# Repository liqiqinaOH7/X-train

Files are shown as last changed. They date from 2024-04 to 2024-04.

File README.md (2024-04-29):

## 圣诞小火车奇遇之旅

这是一份技术文档汇总，主要介绍了圣诞小火车的硬件、机械结构、嵌入式代码等。

- 一些简单的介绍可以通过设计报告、视频和预提交ppt（https://1drv.ms/p/c/84c9984635f4f820/Ec5dhPh6r1hGjR61JKherjkBSfVEN543lnbwKaZI-xJIgA?e=UAQMFG）等方式了解。
- 电源、硬件、机械结构部分详细介绍请访问文档：
https://xn4zlkzg4p.feishu.cn/wiki/TbJOwzE71iRRNpkO2xwcQ5TinEe?from=from_copylink
- 嵌入式部分代码分为小车部分和中控板部分，具体代码在相应文件夹内。
- 机械结构的工程文档（Fusion360）可以在3D_Design文件夹内找到。

English:

This is a summary of the hardware, mechanical structure, and embedded code of the Christmas car.

- Some simple introductions can be obtained by watching design reports, videos, and pre-submitted ppts (https://1drv.ms/p/c/84c9984635f4f820/Ec5dhPh6r1hGjR61JKherjkBSfVEN543lnbwKaZI-xJIgA?e=UAQMFG).
- For more detailed information about power, hardware, and mechanical structure, please visit the documentation: https://xn4zlkzg4p.feishu.cn/wiki/TbJOwzE71iRRNpkO2xwcQ5TinEe?from=from_copylink
- The embedded code is divided into the car and the control board, and the specific code can be found in the corresponding folder.
- The mechanical structure's engineering documentation (Fusion360) can be found in the 3D_Design folder.

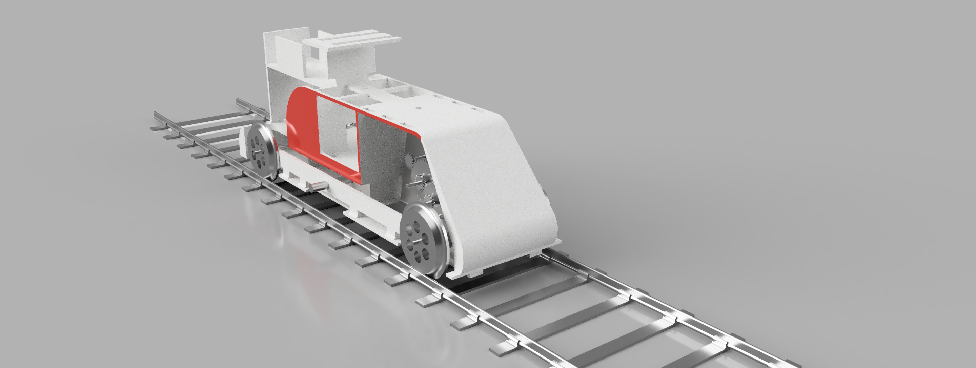
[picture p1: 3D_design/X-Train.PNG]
X-Train


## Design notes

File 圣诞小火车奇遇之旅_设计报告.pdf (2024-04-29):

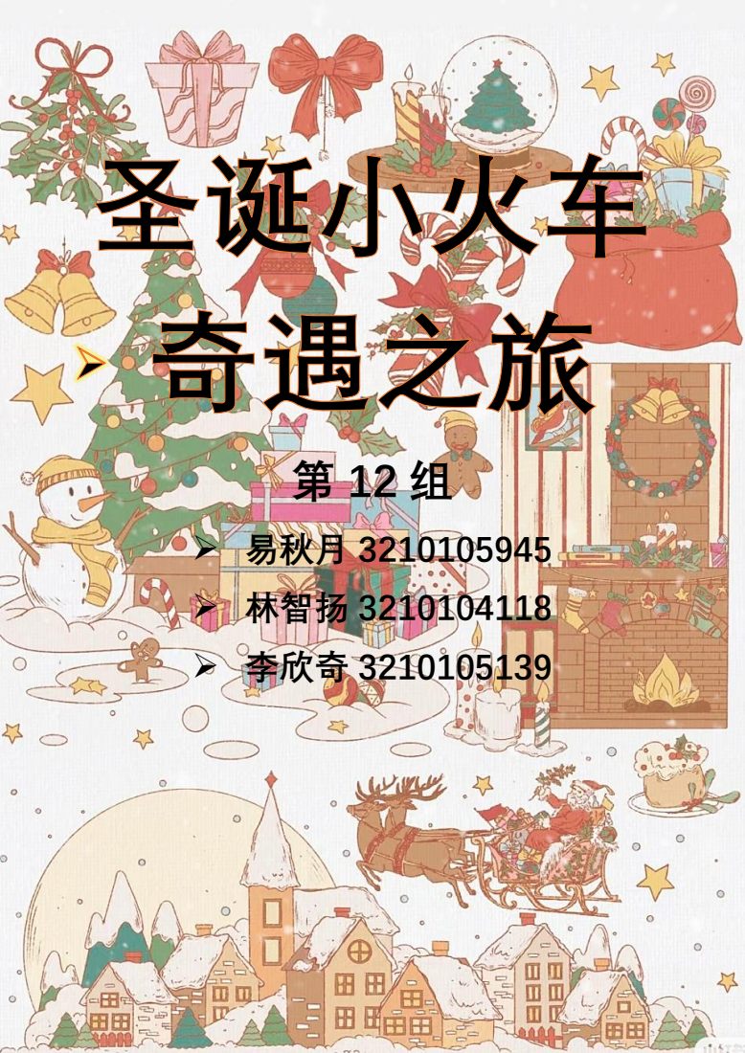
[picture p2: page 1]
➢ 易秋月 3210105945; ➢ 林智扬 3210104118; ➢ 李欣奇 3210105139

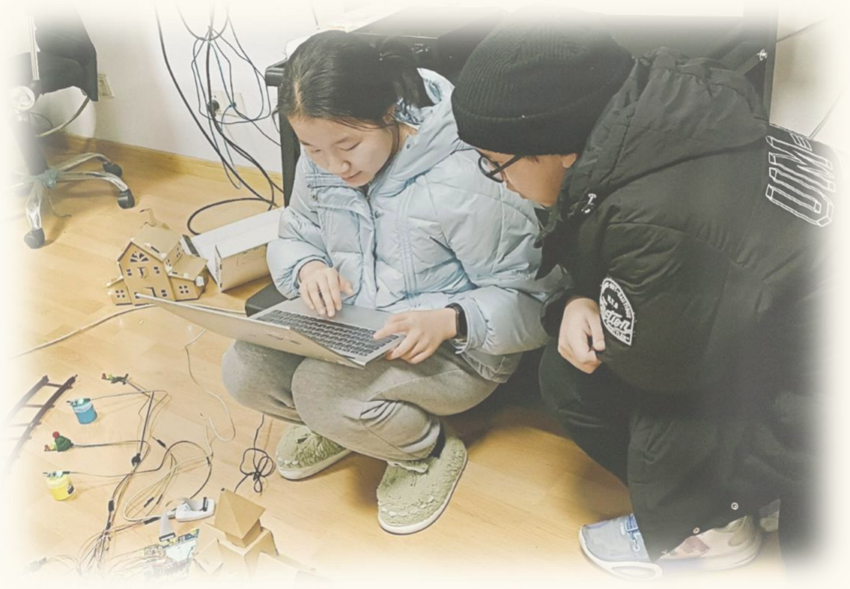
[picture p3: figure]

目录

目录

# 微控制器介绍

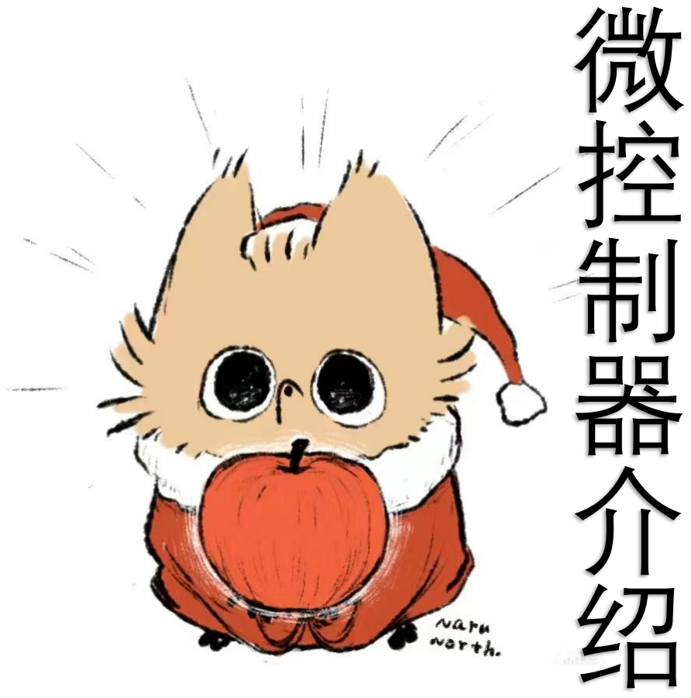
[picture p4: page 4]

## 一、微控制器介绍

1、ARM Cortex-M 系列微控制器概况：

ARM 公司从 ARMv6-ARMv7 时代开始 ARM 开始使用 A、R、M 系列来命名其新的处理器。

A 系列为应用处理器（Application Processor），其中 A 可以理解为 Application，面

向移动计算，智能手机，服务器等市场的的高端处理器。这类处理器运行在很高的时钟频率

（超过 1GHz），支持像 Linux，Android，MS Windows 和移动操作系统等完整操作系统需要

的内存管理单元（MMU）。如果规划开发的产品需要运行上述其中的一个操作系统，需要选择

ARM 应用处理器.

R 系列为实时处理器（Real-time Processors），其中 R 为 RealTime，面向实时应用的

高性能处理器系列，例如硬盘控制器，汽车传动系统和无线通讯的基带控制。多数实时处理

器不支持 MMU，不过通常具有 MPU、Cache 和其他针对工业应用设计的存储器功能。实时处

理器运行在比较高的时钟频率（例如 200MHz 到 >1GHz ），响应延迟非常低。虽然实时处理

器不能运行完整版本的 Linux 和 Windows 操作系统，但是支持大量的实时操作系统（RTOS）。

M系列为微控制器处理器（MicrocontrollerProcessors），其中M指的是Microcontroler

目前主要有 M0、M0+、M3、M4、M7 以及新发布不久的基于 ARMv8-M 构架的 M23、M33，其中

M23 为 M0&M0+的升级，M33 为 M3、M4 的升级。微控制器处理器通常设计成面积很小和能效

比很高。通常这些处理器的流水线很短，最高时钟频率很低（虽然市场上有此类的处理器可

以运行在 200Mhz 之上）。并且，新的 Cortex-M 处理器家族设计的非常容易使用。因此，

ARM 微控制器处理器在单片机和深度嵌入式系统市场非常成功和受欢迎。性能天梯如下图：

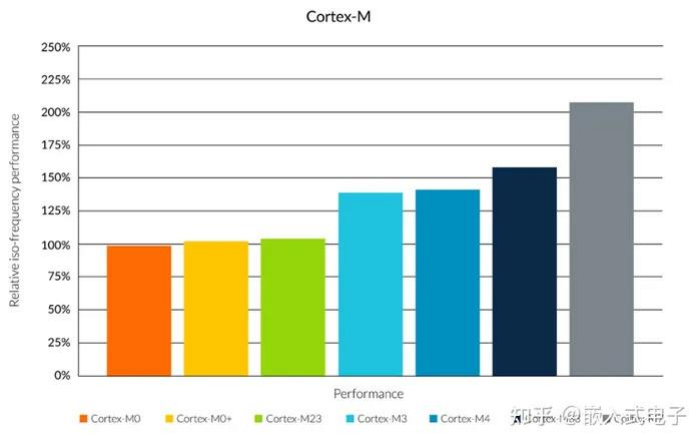
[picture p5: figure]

图 1 性能天梯对比

上图为同等主频下，各个内核可以提供的运算性能的大概的对比关系，评判一个处理器

处理性能一直是一个难题，有很多的评判标准，上图是 ARM 官网提供的，Cortex-M 系列在

ARM 官网上一直以 Coremark 分数为主要评测标准，可作为参考，真实的性能对比需要具体

应用。

2、Cortex-M 处理器家族

Cortex-M 处理器家族更多的集中在低性能端，但是这些处理器相比于许多微控制器使

用的传统处理器性能仍然很强大。例如，Cortex-M4 和 Cortex-M7 处理器应用在许多高性

能的微控制器产品中，最大的时钟频率可以达到 400Mhz。

当然，性能不是选择处理器的唯一指标。在许多应用中，低功耗和成本是关键的选择指

标。因此，Cortex-M 处理器家族包含各种产品来满足不同的需求：

Cortex-M0 | 面向低成本，超低功耗的微控制器和深度嵌入应用的非常小的处理器 (最小 12K 门电路)
Cortex-M0+ | 针对小型嵌入式系统的最高能效的处理器，与 Cortex-M0 处理器接近 的尺寸大小和编程模式但是具有扩展功能，如单周期 I/O 接口和向量 表重定位功能
Cortex-M1 | 针对 FPGA 设计优化的小处理器，利用 FPGA 上的存储器块实现了紧横 合内存 (TCM)。和 Cortex-M0 有相同的指令集
Cortex-M3 | 针对低功耗微控制器设计的处理器，面积小但是性能强劲，支持可以处 理器快速处理复杂任务的丰富指令集。具有硬件除法器和乘加指令 (MAC).并且，M3 支持全面的调试和跟踪功能使软件开发者可以快速的 开发他们的应用
Cortex-M4 | 不但具备 Cortex-M3 的所有功能，并且扩展了面向数字信号处理(DSP) 的指令集，比如单指今多数据指令(SMID)和更快的单周期 MAC 操作此 外，它还有一个可选的支持 IEEE754 浮点标准的单精度浮点运算单元
Cortex-M7 | 针对高端微控制器和数据处理密集的应用开发的高性能处理器。具备 Cortex-M4 支持的所有指令功能，扩展支持双精度浮点运算，并且具备 扩展的存储器功能，例如 Cache 和紧耦合存储器(TCM)
Cortex-M23 | 面向超低功耗，低成本应用设计的小尺寸处理器，和 Cortex-MO 相 似，但是支持各种增强的指令集和系统层面的功能特性。M23 还支持 TrustZone 安全扩展
Cortex-M33 | 主流的处理器设计，与之前的 Cortex-M3 和 Cortex-M4 处理器类似， 但系统设计更灵活，能耗比更高效，性能更高。M33 还支持 TrustZone 安全扩展

3、微处理器为 Cortex-M3 的微控制器 STM32F103ZE

- 核心：STM32F103ZE 采用 ARM Cortex-M3 32 位处理器核心，运行频率高达 72 MHz。
- 存储：具有 512 KB 的闪存存储器和 64 KB 的静态随机存取存储器（SRAM）。
- 外设：包括多个通用定时器、串行通信接口（SPI、I2C）、通用异步收发器（USART）、

模拟-数字转换器（ADC）等。

- 连接：支持多种外部连接接口，如 USB、CAN、以太网等。
- 电源：具有多种电源管理功能，包括低功耗模式和多种电源模式选择。
- 封装：该微控制器的封装形式为 144 引脚 LQFP。

以本课程实验采用的微控制器 STM32F103ZET6 为例：

外观方面，STM32F103ZET6 采用的是 176 引脚的 LQFP 封装，在封装上与其他系列的

STM32 微控制器保持了一致性。该封装形式易于焊接和布局，便于将其集成到具体的应用中。

同时，该封装也提供了丰富的 I/0 引脚，满足了各种应用的需求。

关于性能，STM32F103ZET6 内置了一颗 ARM Cortex-M3 内核，运行频率可高达 72MHz。

该内核具备高性能、低功耗、高集成度等特点，能够满足日常应用中对处理器性能的要求。

此外，其还配备了 256KB 的闪存和 64KB 的 SRAM，可以存储大量的应用程序和数据。同时，

该微控制器还支持种外设接口，如 USB、SPI、I2C 等，便于与其他设备进行通信和扩展。

在应用场景方面，STM32F103ZET6 适用于广泛的应用领域。首先，在工业自动化领域，

该微制器的高性能和丰富的接口能够满足工业控制系统对处理能力和通信能力的要求。其

次，在消费电子领域，STM32F103ZET6 可以用于电视机、空调、音响等产品中，通过各种接

口实现与其他设备的连接和控制。此外，在智能家居领域，该微控制器可以作为智能家居控

制主板，实现对家居设备的管理和控制。另外，在智能交通领域，STM32F103ZET6 可以用于

交通信号灯、ETC 系统等设备，实现车辆和设备的智能化控制。总之，STM32F103ZET6 具有

广泛的应用领域，并且能够满足不同领域中对处理器性能和通信能力的要求

除了上述介绍的特点外，STM32F103ZET6 还具有其他一些重要的特性。首先，它支持多

种电源模式，包括 Halt、Stop、Standby 等模式，以满足不同应用对功耗的要求。其次，该

微控制器具备强大的中断系统，可实现多个外设的优先级管理和中断处理。此外，

STM32F103ZET6 还具备丰富的时钟系统和时钟源，能够满足不同应用对时钟稳定性和精确性

的需求。

综上所述，STM32F103ZET6 是一款性能卓越的 32 位 ARM Cortex-M3 微控制器。其具备

高性能、低功耗、丰富的接口等特点，适用于广泛的应用场景。无论是工业控制、消费电子、

智能家居还是智能交通等领域，STM32F103ZET6 都能够提供稳定可靠的处理能力和通信能力，

满足各种应用的需求。同时，其外观封装简便易用，适合在各种应用中集成使用。

# 编程工具/软件开发平台

# 对比与选择

## 二、编程工具/软件开发平台的对比与选择

1、Keil

1）集成开发环境（IDE）：Keil 提供了一个全面的集成开发环境，包括编辑器、编译器、调

试器和仿真器，使开发人员可以在一个统一的界面中进行嵌入式软件开发。

2）支持多种嵌入式平台：Keil 支持多种嵌入式平台，包括 ARM、8051 和 C166 等，可以方

便地开发不同类型的嵌入式系统。

3）强大的编译器：Keil 提供了高效的编译器，可以生成高质量的机器代码，优化程序性能

和内存占用。

4）丰富的调试功能：Keil 具有强大的调试功能，可以进行单步调试、断点调试、变量监视

5）等，帮助开发人员快速定位和修复问题。

6）支持多种编程语言：Keil 支持多种编程语言，包括 C、C++和汇编语言，可以根据开发需

求选择适合的编程语言。

7）生态系统支持：Keil 有一个庞大的生态系统，包括广泛的开发者社区、技术支持和第三

方工具支持，可以帮助开发人员更好地应对嵌入式开发挑战。

2、IAR

1）跨平台支持：IAR 可以在多个操作系统上运行，包括 Windows 和 Linux。

2）多种编程语言支持：IAR 支持多种编程语言，包括 C、C++和汇编语言。

3）优化编译器：IAR 提供了高度优化的编译器，可以生成高效的嵌入式代码，以提高系统性

能和节省存储空间。

4）调试功能：IAR 集成了强大的调试功能，包括源码级调试、断点设置、变量监视等，可以

5）帮助开发人员快速定位和解决问题。

6）仿真器支持：IAR 支持多种仿真器和调试器，可以与各种硬件平台进行无缝集成。

7）丰富的库支持：IAR 提供了丰富的软件库，包括通信协议、驱动程序和算法库等，可加快

开发速度。

8）可扩展性：IAR 支持插件和扩展，可以根据项目的需求进行定制和扩展。

3、STM32CubeIDE

1）基于 Eclipse 平台，提供了强大的代码编辑器、调试器和构建系统。

2）集成了 STM32CubeMX，一个图形化配置工具，用于快速生成 STM32 的初始化代码和配置

文件。

3）支持多种编译器和调试器，如 GCC、IAR Embedded Workbench、ST-Link 等。

4）提供了丰富的调试功能，包括实时变量查看、断点设置、跟踪等。

5）支持版本控制系统，如 Git，方便团队协作和代码管理。

6）提供了丰富的示例代码和应用程序模板，加速开发过程。

综合上述列举 3 个编程工具的特点，我们对其功能进行如下评价：

功能评价 | Keil | IAR | STM32CubeIDE
中断调试 | 支持 | 支持 | 支持
AAPCS 规范的 C/C++ 与汇编混合编程 | 支持 | 支持 | 支持
MCU 与外部电路的 模拟 | 支持 | 不支持 | 支持
优点 | 1.老牌 IDE，教程较 多，容易找到各种问 题的解决办法；2.基 于Keil的软件工程参 考资料多 | 1.提供了丰富的文 档资料和技术支持； 2.操作界面进行了 现代化改进，直观清 晰 | 1.ST 官方软件，对 STM32 开发友好；2. 基于 Eclispse 工具 链，界面更现代化
缺点 | 1.界面不现代化；2. 编辑功能有待改善 | 1.工具链闭源，限制 了对工具本身的的 定制和扩展；2.操作 难度相对较高 | 1.推出时间不长，存 在一些问题；2.相对 Keil 更耗电脑 CPU 资源

通过以上对比分析，我们最后选择 Keil 作为主要编程工具。

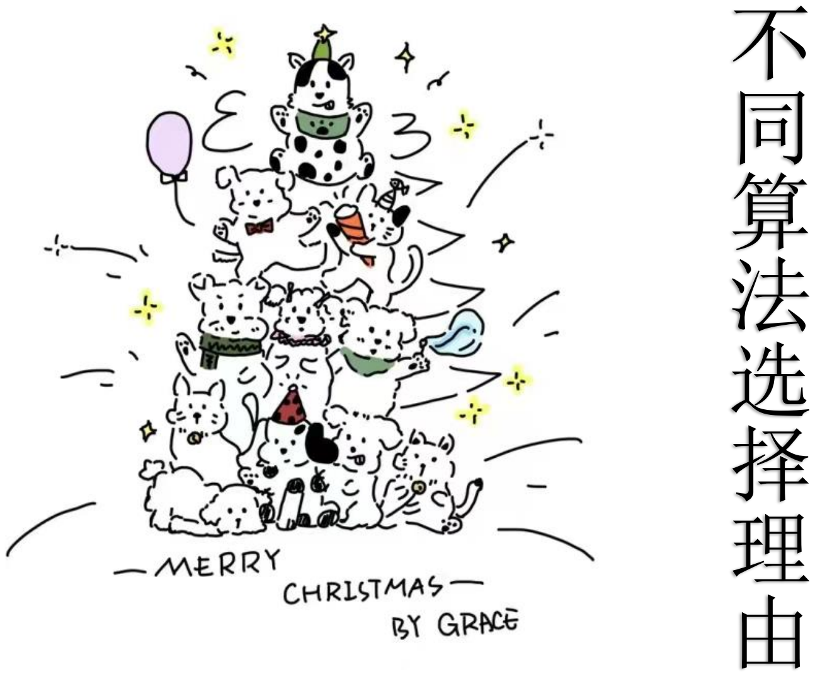
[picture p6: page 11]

# 不同算法选择理由

## 三、不同算法选择理由

由于本项目的代码部分相对较少，涉及的核心算法只有速度检测算法，因此这里重点探

讨速度检测算法的算法选择。

1、帧间差分法

对视频序列进行物体检测和跟踪，获取物体在连续帧中的位置信息。计算相邻帧之间物

体位置的差异，可以使用欧氏距离或其他相似度度量方法。将差异除以时间间隔，得到物体

的平均速度。

当视频中存在移动物体的时候，相邻帧（或相邻三帧）之间在灰度上会有差别，求取两

帧图像灰度差的绝对值，则静止的物体在差值图像上表现出来全是 0，而移动物体特别是移

动物体的轮廓处由于存在灰度变化为非 0，当绝对值超过一定阈值时，即可判断为运动目标，

从而实现目标的检测功能。 帧间差分法的优点是算法实现简单，程序设计复杂度低；对光

线等场景变化不太敏感，能够适应各种动态环境，有着比较强的鲁棒性。缺点是不能提取出

对象的完整区域，对象内部有“空洞”，只能提取出边界，边界轮廓比较粗，往往比实际物

体要大。对快速运动的物体，容易出现鬼影的现象，甚至会被检测为两个不同的运动物体，

对慢速运动的物体，当物体在前后两帧中几乎完全重叠时，则检测不到物体。故该方法一般

适用于简单的实时运动检测的情况。

2、DeepSORT 目标跟踪算法

DeepSORT（Deep Learning + SORT）是一种基于深度学习和卡尔曼滤波的目标跟踪算

法。它通过结合 YOLOv5 等目标检测器的输出和 SORT（Simple Online and Realtime Tracking）

算法的轨迹管理，实现对视频中目标的准确跟踪。使用深度学习模型（如 ResNet）提取目标

的特征向量，将其用于目标的身份验证和关联。使用卡尔曼滤波器来预测目标的位置和速度，

并通过将检测和预测结果进行关联，提供平滑的目标轨迹。使用匈牙利算法将当前帧的检测

结果与上一帧的跟踪结果进行关联，以最大化目标标识的一致性。

它结合了卷积神经网络(CNN)和递归神经网络(RNN)的优势，能够在复杂背景下跟踪多个

目标。DeepSORT 算法包含三个部分:目标检测、特征提取和目标跟踪。

首先，DeepSORT 通过目标检测算法(如 YOLO、Faster R-CNN 等)检测出图像中的目标，

并使用卷积神经网络从目标中提取特征。接下来，使用递归神经网络(LSTM) 对目标进行跟

踪，并根据目标的运动状态更新目标的状态。与传统的目标跟踪算法相比，DeepSORT 具有

更高的准确性和效率，并且可以跟踪多个目标。它在许多实际场景中得到了广泛应用，如视

频监控、自动驾驶、人机交互等。

3、传感器测速

3.1 车辆传感器

霍尔效应：速度传感器中包含一个霍尔元件，当车轮转动时，通过车轮上的齿轮或者磁

铁，产生的磁场变化会影响霍尔元件，从而产生电压信号。根据这些信号的频率或脉冲数，

可以计算出车辆的速度。

磁阻效应：另一种常见的方法是利用磁阻传感器。在车轮上安装有磁性的传动齿轮，当

车轮旋转时，磁阻传感器感知到磁场的变化，产生相应的电压信号。通过测量这些信号的变

化，可以计算出车辆的速度。

3.2 轨道传感器

传感器固定在轨道上，监测每个轨道区间的状况，当出现变化时判定为列车经过，从而

检测列车的位置和速度。

在速度检测方式的选择上，常见的速度检测方式主要包括雷达测速、激光测速、视频测

速、车载 GPS 测速、传感器测速等，由于本实验的成本有限，开发板的处理器和内存大小有

限，硬件设施受到许多制约，不能采用最初设想的使用外接摄像头模块，基于深度学习从摄

像头拍摄的实时视频中进行目标追踪从而准确计算列车速度的方式，因此我们将目光转向了

成本更低、操作方式更简单、实现难度更低的传感器测速方式。

在传感器的选择上，出于成本考虑，我们采购的红外传感器模块功能相对较为简单，输

出信号只有高低电平之分，没有具体数值和其他有参考价值的信息，因此我们决定将传感器

按照区间固定在轨道上，当列车经过时根据传感器持续输出高电平的时间来估计列车的平均

速度。

# C/C++与汇编语言代码编写规范

## 四、C/C++与汇编语言代码编写规范

广为采用的编码规范：

- GNU Coding Standards
- Guidelines for the Use of the C Language in Vehicle Based Software
- C++ Coding Guidelines
- SUN Code Conventions for Java

1、C/C++代码编写规范

（1）文件排版方面

①包含头文件

1.1 先系统头文件，后用户头文件。

1.2 系统头文件，稳定的目录结构，应采用包含子路径方式。

1.3 自定义头文件，不稳定目录结构，应在 dsp 中指定包含路径。

1.4 系统头文件应用：#include <xxx.h>

1.5 自定义同文件应用：#include "xxx.h"

1.6 只引用需要的头文件。

②h 和 cpp 文件

2.1 头文件命名为*.h，内联文件命名为*.inl；C++文件命名为*.cpp

2.2 文件名用大小写混合，或者小写混合。例如 DiyMainview.cpp，infoview.cpp。不要用

无意义的名称：例如 XImage.cpp；SView.cpp；xlog.cpp；

2.3 头文件除了特殊情况，应使用#ifdef 控制块。

2.4 头文件#endif 应采用行尾注释。

2.5 头文件，首先是包含代码块，其次是宏定义代码块，然后是全局变量，全局常量，类型

定义，类定义，内联部分。

2.6 CPP 文件，包含指令，宏定义，全局变量，函数定义。

③文件结构

3.1 文件应包含文件头注释和内容。

3.2 函数体类体之间原则上用 2 个空行，特殊情况下可用一个或者不需要空行。

④空行

4.1 文件头、控制块，#include 部分、宏定义部分、class 部分、全局常量部分、全局变量

部分、函数和函数之间，用两个空行。

（2）注释方面

①文件头注释

1.1 作者，文件名称，文件说明，生成日期(可选)

②函数注释

2.1 关键函数必须写上注释，说明函数的用途。

2.2 特别函数参数，需要说明参数的目的，由谁负责释放等等。

2.3 除了特别情况，注释写在代码之前，不要放到代码行之后。

2.4 对每个#else 或#endif 给出行末注释。

2.5 关键代码注释，包括但不限于：赋值，函数调用，表达式，分支等等。

2.6 善未实现完整的代码，或者需要进一步优化的代码，应加上 // TODO ...

2.7 调试的代码，加上注释 // only for DEBUG

2.8 需要引起关注的代码，加上注释 // NOTE ...

2.9 对于较大的代码块结尾，如 for,while,do 等，可加上 // end for|while|do

（3）命名方面

①原则

1.1 同一性：在编写一个子模块或派生类的时候，要遵循其基类或整体模块的命名风格，保

持命名风格在整个模块中的同一性。

1.2 标识符组成：标识符采用英文单词或其组合，应当直观且可以拼读，可望文知意，用词

应当准确，避免用拼音命名。

1.3 最小化长度 && 最大化信息量原则：在保持一个标识符意思明确的同时，应当尽量缩

短其长度。

1.4 避免过于相似：不要出现仅靠大小写区分的相似的标识符，例如"i"与"I"，"function"

与"Function"等等。

1.5 避免在不同级别的作用域中重名：程序中不要出现名字完全相同的局部变量和全局变

量，尽管两者的作用域不同而不会发生语法错误，但容易使人误解。

1.6 正确命名具有互斥意义的标识符：用正确的反义词组命名具有互斥意义的标识符，如：

"nMinValue" 和 "nMaxValue"，"GetName()" 和"SetName()" ….

1.7 避免名字中出现数字编号：尽量避免名字中出现数字编号，如 Value1,Value2 等，除非

逻辑上的确需要编号。这是为了防止程序员偷懒，不肯为命名动脑筋而导致产生无意义的名

字（因为用数字编号最省事）。

（4）代码风格方面

①Tab 和空格

1.1 每一行开始处的缩进只能用 Tab，不能用空格，输入内容之后统一用空格。除了最开始

的缩进控制用 Tab，其他部分为了对齐，需要使用空格进行缩进。这样可以避免在不同的编

辑器下显示不对齐的情况。

1.2 在代码行的结尾部分不能出现多余的空格。

1.3 不要在"::","->","."前后加空格。

1.4 不要在"，","；"之前加空格。

②类型定义和{

2.1 类，结构，枚举，联合：大括号另起一行

③函数

3.1 函数体的{需要新起一行，在{之前不能有缩进。

3.2 除了特别情况，函数体内不能出现两个空行。

3.3 除了特别情况，函数体内不能宏定义指令。

3.4 在一个函数体内，逻揖上密切相关的语句之间不加空行，其它地方应加空行分隔。

3.5 在头文件定义的 inline 函数，函数之间可以不用空行，推荐用一个空行。

④代码行

4.1 一行代码只做一件事情，如只定义一个变量，或只写一条语句。这样的代码容易阅读，

并且方便于写注释。

4.2 多行变量定义，为了追求代码排版美观，可将变量竖向对齐。

4.3 代码行最大长度宜控制在一定个字符以内，能在当前屏幕内全部可见为宜。

⑤宏

5.1 不要用分号结束宏定义。

5.2 函数宏的每个参数都要括起来。

5.3 不带参数的宏函数也要定义成函数形式。

（5）类型

定义指针和引用时*和&紧跟类型。

尽量避免使用浮点数，除非必须。

用 typedef 简化程序中的复杂语法。

避免定义无名称的类型。例如：typedef enum { EIdle, EActive } TState;

少用 union，如果一定要用，则采用简单数据类型成员。

用 enum 取代(一组相关的)常量。

不要使用魔鬼数字。

尽量用引用取代指针。

定义变量完成后立即初始化，勿等到使用时才进行。

如果有更优雅的解决方案，不要使用强制类型转换。

（6）性能

使用前向声明代替#include 指令。Class M;

尽量用++i 代替 i++。即用前缀代替后缀运算。

尽量在 for 循环之前，先写计算估值表达式。

尽量避免在循环体内部定义对象。

避免对象拷贝，尤其是代价很高的对象拷贝。

避免生成临时对象，尤其是大的临时对象。

注意大尺寸对象数组。

80-20 原则。

（7）兼容性

遵守 ANSI C 和 ISO C++国际标准。

确保类型转换不会丢失信息。

注意双字节字符的兼容性。

注意运算溢出问题。

不要假设类型的存储尺寸。

不要假设表达式的运算顺序。

不要假设函数参数的计算顺序。

不要假设不同源文件中静态或全局变量的初始化顺序。

不要依赖编译器基于实现、未明确或未定义的功能。

将所有#include 的文件名视为大小写敏感。

避免使用全局变量、静态变量、函数静态变量、类静态变量。在使用静态库，动态库，多线

程环境时，会导致兼容性问题。

不要重新实现标准库函数,如 STL 已经存在的。

2、汇编语言代码编写规范

（1）文件结构

每个汇编程序通常分为两个文件。一个文件用于保存程序的声明（declaration），称为

头文件。另一个文件用于保存程序的实现（implementation），称为定义（definition）文

件。头文件以“.h”为后缀，定义文件以“.asm”为后缀,宏定义文件以“.mac”为后缀。

1.1 头文件

用 .include di.h 头文件（编译器将从用户的工作目录开始搜索）。

每个标号定义时,要加空格时都用”Tab”键,定义符和定义值要整齐,每个定义符后都在同

一列加上”;”(分号),分号后加上每个标号的注释。

1.2 函数

原则上函数内不允许对绝对地址进行操作。

函数内不要分配大的数组，占用堆栈空间。

函数内尽量不要使用数字和字符等常量，而要用标识符常量，便于以后的修改。

每个函数体不得超过 150 行（不含注释）

（2）程序的版式

2.1 对齐

要求编辑中对齐使用 Tab，而编辑软件中将 Tab 设为 8 个字符位置，且跳格不用空格代替。

每行程序宽度为 6 个 Tab 宽,即 8*6=48 个字符,第 49 列为分号,分号后写注释。

标号从行首(即第 1 列)开始输入,标号后不直接跟汇编指令,换行后加一个 Tab 键后再输入

汇编助记符,输完助记符后再加一个 Tab 键才输操作数。

2.2 注释

使用中文做注释。

汇编语言是低级语言,原则上要求每行都加上注释。最少注释率不得低于 50%。

边写代码边注释，修改代码同时修改相应的注释，以保证注释与代码的一致性。不再有用的

注释要删除。

注释应当准确、易懂，防止注释有二义性。错误的注释不但无益反而有害。

尽量避免在注释中使用缩写，特别是不常用缩写。

注释的位置应与被描述的汇编指令相邻，汇编语言一般把注释放在指令的右方。 （3）命名规则
标识符应当直观且可以拼读，可望文知意，不必进行“解码”。 标识符最好采用英文单词或其组合，便于记忆和阅读。切忌使用汉语拼音来命名。 程序中的英文单词一般不会太复杂，用词应当准确。例如不要把 CurrentValue 写成 NowValue。
单词连写时,用第一个字母大写来区分。如: CurrentValue。

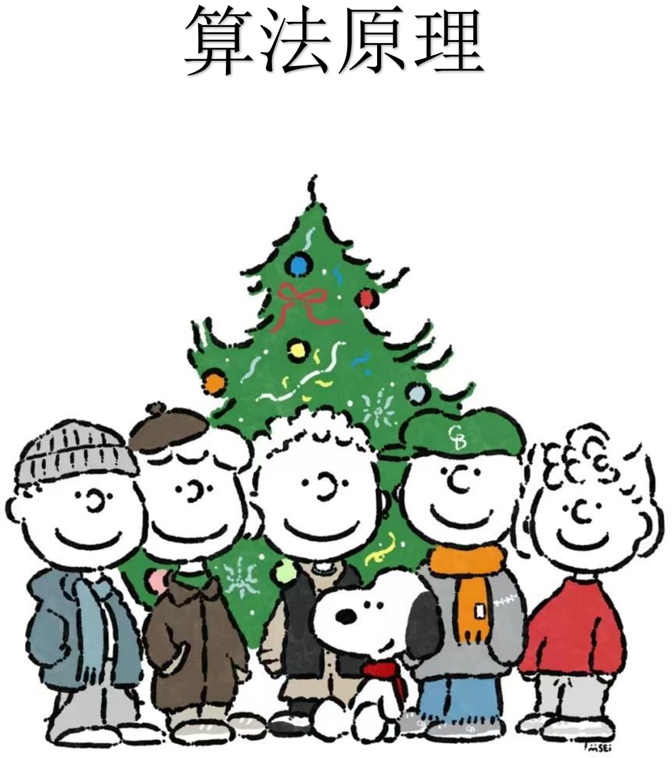
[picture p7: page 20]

# 算法原理

## 五、算法原理

基于红外传感器的 STM32 速度检测算法：

1、红外传感器模块工作原理

红外接近传感器或红外传感器它发射红外光以感知周围环境，并可用于检测物体的运动。

由于这是一个无源传感器，它只能测量红外辐射。

VCC 连接到 开发板上的 5V 引脚的红外传感器的电源引脚。

OUT 引脚为 5V TTL 逻辑输出。低表示未检测到运动;高表示检测到运动。

GND 连接到开发板的接地引脚。

它由两个主要组件组成：第一个是红外发射器部分，第二个是红外接收器部分。在发射

器部分，使用红外 LED，在接收器部分，光电二极管用于接收红外信号，经过信号处理和调

理，将获得输出。红外传感器的工作原理是向红外发光二极管施加电压，红外发光二极管发

出红外光。该光在空气中传播并撞击物体，然后光电二极管传感器接收。如果物体近，反射

光会更强，如果物体离得远，反射光会更弱当传感器触发时，它通过输出引脚发送低电平，

任何类型的微控制器都可以检测到该信号以执行特定任务。该模块内置了两个板载 LED，其

中一个在电源可用时亮起，另一个在电路被触发时打开。该传感器功耗低、成本低、坚固耐

用，并且具有宽感应范围，可以调整灵敏度。红外传感器模块可由 3.3V 和 5V 电源供电，

传感器可测量的距离为 2-10 厘米。

2、实时速度计算

采用公式速度=路程/时间进行计算，将红外传感器垂直于轨道放置，当红外传感器检测

到信号时启动计时器开始计时，当未检测到信号时停止计时，记录这段时间的长度，在这段

时间内列车走过的路程即为列车本身的长度，路程÷时间即可得到这段区间内列车的平均速

度。

3、实时速度哈希演算

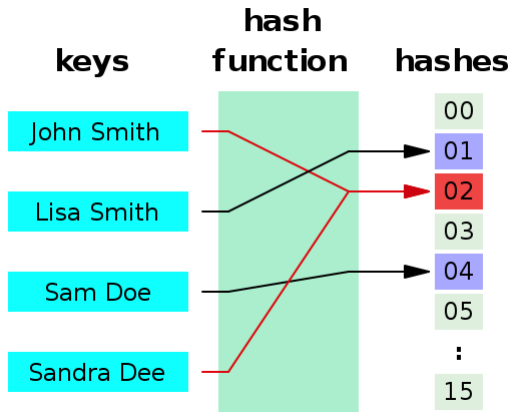
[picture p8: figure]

哈希算法(Hash Function)，将任意长度的二进制值串映射为固定长度的二进制值串，

这个映射的规则就是哈希算法，而通过原始数据映射之后得到的二进制值串就是哈希值。构

成哈希算法的条件：从哈希值不能反向推导出原始数据（所以哈希算法也叫单向哈希算法）；

对输入数据非常敏感，哪怕原始数据只修改了一个 Bit，最后得到的哈希值也大不相同；散

列冲突的概率要很小，对于不同的原始数据，哈希值相同的概率非常小；哈希算法的执行效

率要尽量高效，针对较长的文本，也能快速地计算出哈希值。在实验中该算法主要用于速度

预测与检验功能。

## 六、外部电路实现

1. 总览

小车：

1) 列车建模及加工
2) STM32F103C8T6 主控制器（最小系统板）
3) R280 电机
4) HC-05 蓝牙模块
5) 18650 电池 3 节

主控制器（STM32F103ZET6）：

1) 中控屏
2) 信号灯模块 5 个
3) 红外传感器模块 5 个
4) HC-05 蓝牙模块
2. 机械设计部分

主要结构：

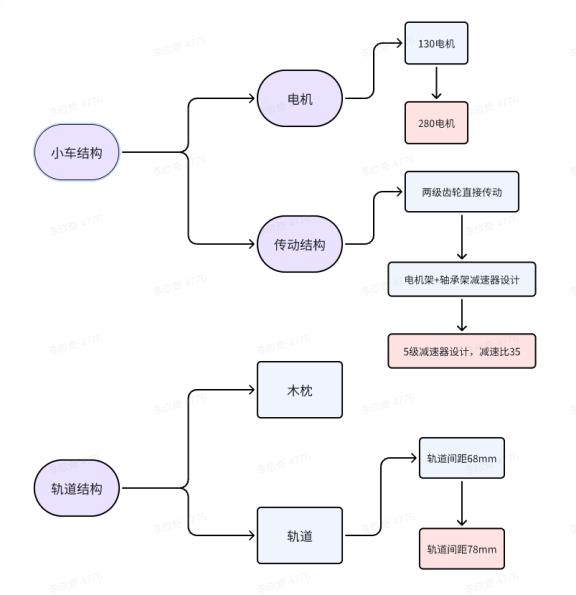
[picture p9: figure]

1. 设计原理

总体来讲，小火车运动的能量来源是位于后舱底部的两节 9250mWh 容量的 18650 锂电池串

联得到的 7.4V-8.4V 电压。电池给 L298N 电机驱动模块供电（要求 VCC 大于 5V），L298N 把

从单片机得到的 PWM 信号电流放大后输出给电机，使电机达到预定转速和扭矩。而小火车的

轮子采用圆台结构，圆台侧面与粘贴了胶条的轨道表面接触，将前车轮轴的旋转运动转化为

小火车的线性运动。需要注意的是，由于圆台侧面内外的周长不同，小火车可以根据转弯半

径自动调节接触点位置，当接触点位于外侧时，周长小，转化成的线速度小；当接触点位于

内侧时，周长大，转化成的线速度大。小火车可以基于此原理实现差速转弯。

2. 主体结构
i. 车体架构

车体整体由底板、电机架、减速器（由 3 级双齿轮和轴组成）、前轮轴（驱动轴）、后轮轴（从

动轴）、车轮和各种连接件（如轴承、垫片等）组成。

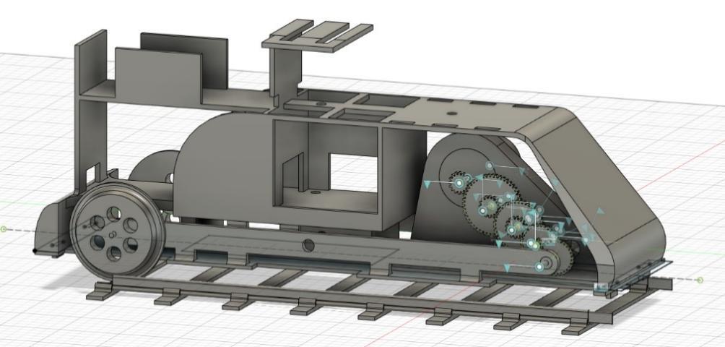
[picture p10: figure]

其中，车架设计了后舱两个，用于存放 18650 锂电池。后舱下部（48*80）存放 2 节 18650，

用于电机驱动模块供电；上部存放 1 节，用于给单片机供电。车架中部下层存放 L298N 电机

驱动模块（45*45），第二层存放电源管理模块（3.7-5V USB），第三层存放 STM32F103C8T6

最小系统板单片机。第二层前部可以用来固定蓝牙模块和未来的拓展模块。

ii. 电动机安装位置

电机安装在小火车前部底层，通过电机架固定在底板上，电机架上同时还留有减速器中各轴

的轴承孔（5）和轴孔（2.5mm 孔 2mm 轴）。轴中心连线与水平线成 45°角。

iii. 传动系统

本设计使用了五级级联齿轮减速器，将驱动力级联或串联，通过多组齿轮间的啮合（一个大

齿轮驱动另一小齿轮）来实现减速，这样组合可以得到较大的减速比。

减速器将 R280 电机提供的 8000+ r/min 的高转速减速到合理的范围内。根据减速器实际的

采用齿轮齿数：

轴#1 | 轴#2 | 轴#3 | 轴#4 | 轴#5
16 | 48-20 | 36-16 | 30-8 | 28

计算得传动比=（48/16）*（36/20）*（30/16）*（28/8）≈35

因此，在圆台的截面圆直径范围为 24-34mm 范围下，可以计算到当电机满功率运行时，内外

最大线速度分别为 287mm/s 和 407mm/s。

iv. 轮子和轴等连接件

轮子：

轮子侧面由轮缘和正常的圆台侧面组成，其中车轮最外侧直径

24.721mm，轮缘和圆台交界处直径 34.187mm。轮缘的作用是将小火

车底部固定在轨道以内，防止火车脱轨。

轴：

全车使用的所有轴都采用 2mm 直径的钢轴，但实际使用发现其很容易形变，以后的机械设计

可以考虑更粗的轴。

齿轮：

齿轮模数采用的是 0.5，齿轮的一些关键参数如下：

模数：直径/齿数；只有模数相等的齿轮才能流畅与运行。

传动比：齿数之比（被动/主动）

压力角：常见的有 20°

中心距：M*（n1+n2）/2

轴承：

采用 682zz 轴承，尺寸为 2*5*2.5；内径为 2mm，外径 5mm，厚度 2.5mm。

v. 轨道和木枕
1. 轨道间距设计

实测火车轮轴内测间距 66~69mm（轮缘内侧间距），外侧间距 80~84mm。最大轨距不超过 80mm

可 保 证 火 车 不 掉 。 理 想 的 接 触 点 间 距 | 75mm | 左 右 。

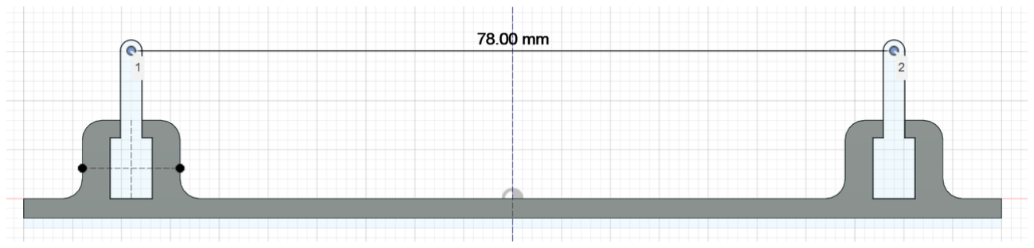
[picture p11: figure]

设计轨道中心点间距 78mm。由于轨道表面会贴 1mm 厚的胶条（增大摩擦力），实际接触点间

距大约在 74~78mm。

2. 加工方式

木枕、轨道的加工采用零件化的方式，这样转移、拼接会方便很多。此外，还可以通过调整

一个个的木枕和轨道的角度自定义地改变轨道的弯曲角度和方向，对于后期改变路线很有帮

助。

3. 连接方式

木枕与轨道的连接几乎是不可拆卸连接，而轨道与轨道的连接（卡扣式）则是可拆卸连接。

对于拼接方式，由于是榫卯连接，不同连接部位的可拆卸性不同，最后采用了至多左右 2 轨

道+若干木枕的方式存储和拼接零件，这样拼接、拆卸方便，工作量不大，且可转移性也比

较高。

3. 硬件电路部分
1. 主控板（STM32F103ZET6）
模块名 | 作用 | 个数 | 协议 | 引 脚 接 口 个 数
红外传感模块 | 感知列车位置 | 5 | I2C/串口 | 1
信号灯模块 | 指示状态及自定义控制 | 5 | 串口 | 3
蓝牙模块 | 对小火车行为下命令 | 1 | 串口 | 2
红外传感模块 | 信号灯模块 | HC-05 蓝牙模块

引脚对应表：

模块名 | 类型 | 引脚 | 模块名 | 类型 | 引脚
信号灯 1 – Green | OUT | PF6 | 传感器 1 | IN | PC3
信号灯 1 – Yellow | OUT | PC13 | 传感器 2 | IN | PC1
信号灯 1 – Red | OUT | PE0 | 传感器 3 | IN | PA5

信号灯 2 – Green | OUT | PC4 | 传感器 4 | IN | PA6
信号灯 2 – Yellow | OUT | PF12 | 传感器 5 | IN | PC2
信号灯 2 – Red | OUT | PF11 | 信号灯 4 – Yellow | OUT | PC0
信号灯 3 – Green | OUT | PD6 | 信号灯 4 – Red | OUT | PF13
信号灯 3 – Yellow | OUT | PE1 | 信号灯 5 – Green | OUT | PF8
信号灯 3 – Red | OUT | PG15 | 信号灯 5 – Yellow | OUT | PF7
信号灯 4 – Green | OUT | PA7 | 信号灯 5 – Red | OUT | PF9

蓝牙模块接口为 PA9（TX），PA10（RX）。

2. 小车板（STM32F103C8T6）
模块名 | 作用 | 个数 | 引 脚 接 口 个 数 | 类型
L298N 模块 | 驱动电机 | 1 | 1 | OUT（PA6）
BOOST 模块 | 将锂电池的 3.7V 转化为 5V | 1 | 0 | /
蓝牙模块 | 接受中控板发出的信号 | 2 | 2 | /

# 设计与调试技巧

## 七、设计技巧

1、列车

1）功能分析：在设计小车结构之前，明确小车的功能需求，本项目中小车采用类火车结构，

需要在列车轨道上运行，并且需要与最小系统板连接，需要提前预留出对应空间。

2）供电模块：小车的供电模块包括电池、电机、驱动电路等。在设计时需要考虑电源的稳

定性、电机的功率与效率，以及驱动电路的控制方式。

3）结构材料选择：根据设计需求和制造成本，选择合适的结构材料，如金属、塑料、碳纤

维等。由于我们采用 3D 打印的方式进行制造，材料选择空间较小，承重为第一考虑因素。

2、轨道

1）系统集成：轨道结构设计需要与之前的列车设计相匹配，确保轨道与车辆的匹配度，从

而提高列车的平稳性和安全性，降低脱轨的风险；

2）结构设计：结构设计需要考虑承载能力、几何形状、连接方式等。主要包括轨道的横断

面设计、轨道连接方式以及轨道的支撑结构。

3）弯道设计：需要考虑列车的最大行驶速度、列车的车长等因素，弯道弧度过大会导致列

车极易脱轨，弧度过小会导致轨道过长，占据空间过大。

3、中控屏

1）时序设计：TFTLCD 屏幕需要精确的时序控制。在设计时需要确保微控制器的时钟频率和

外设时序要求相匹配。时序的不匹配可能导致屏幕显示异常或者不稳定。

2）显示控制：需要编写适配于具体 TFTLCD 屏幕的显示驱动程序。负责将显示数据转换为屏

幕可识别的格式，并通过合适的接口（如并行接口或 SPI 接口）发送数据到屏幕。除此之外

还需要控制屏幕的刷新率以确保显示内容的稳定性和流畅性。这需要结合显示驱动程序和微

控制器的性能来进行优化。

3）显示优化：针对 STM32F103ZET6 的资源限制，需要优化显示数据的处理和存储，以最大

程度地节约微控制器的资源。如在数据存储上需要选择适当的数据结构来组织和存储显示数

据以确保高效的访问和处理。对于需要频繁更新显示的实时数据需要设计高效的数据处理算

法以确保及时更新并减少对微控制器资源的占用。由于屏幕空间有限，在设计过程中还需要

精简显示内容以确保信息的清晰度和可读性。

## 八、调试技巧

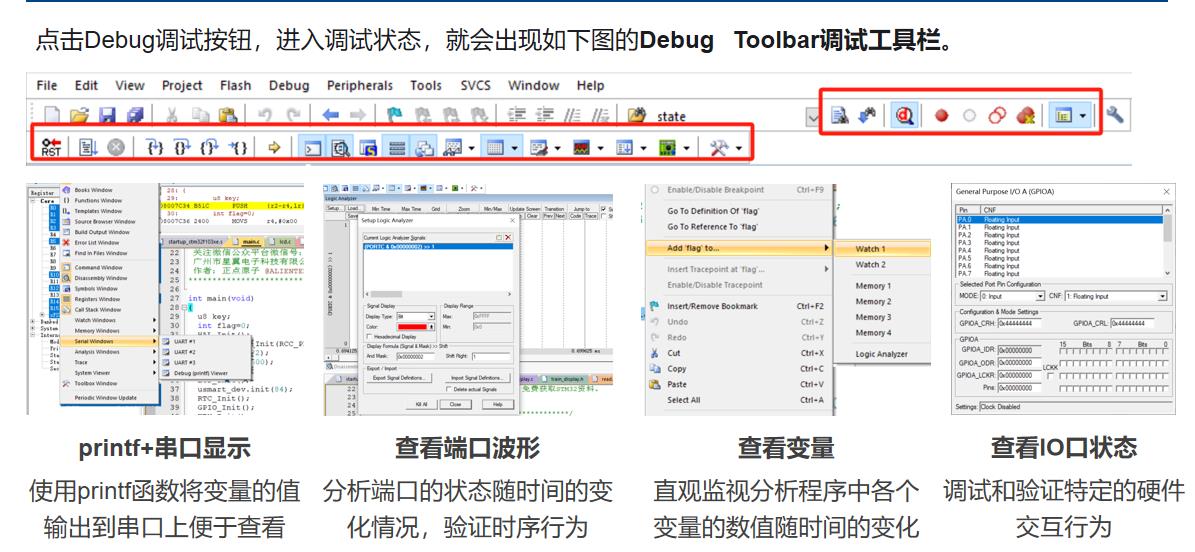
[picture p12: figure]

- Printf+串口显示
在使用 Keil 仿真时想要查看程序的打印信息，主要有两种方法。方法一：使用 keil 自带的 Debug（printf）viewer 窗口打印；方法二：使用串口打印。
一、方法一：使用 keil 自带的 Debug（printf）viewer 窗口打印
Serial windows 窗口——选择 Debug（printf）Viewer 窗口

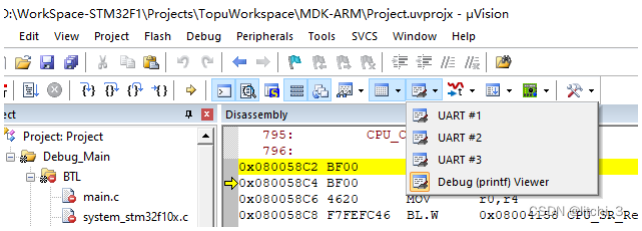
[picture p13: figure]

将 printf 函数重定向到 ITM 口，在程序中添加相关代码
#define ITM_Port8(n) | (*((volatile unsigned char *)(0xE0000000+4*n)))

#define ITM_Port16(n) | (*((volatile unsigned short*)(0xE0000000+4*n)))

#define ITM_Port32(n) | (*((volatile unsigned long *)(0xE0000000+4*n)))

#define DEMCR | (*((volatile unsigned long *)(0xE000EDFC)))

#define TRCENA | 0x01000000

struct __FILE { int handle; /* Add whatever is needed */ };
FILE __stdout;
FILE __stdin;

int fputc( int ch, FILE *f ) { if (DEMCR & TRCENA)
{

while (ITM_Port32(0) == 0); ITM_Port8(0) = ch;
}
return(ch);
}
代码添加完成后打开魔术棒的 Debug 窗口，调试器选择后，打开 setting 窗口，选择 Trace， 配置 ITM Stimulus Ports 后，使能相应 port。
配置好后进行仿真，查看 Debug(printf) Viewer 窗口，可以看到调试信息。

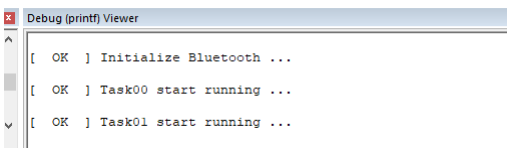
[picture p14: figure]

二、方法二：重定向到串口打印
使用 fputc 函数重定向到串口打印
- 查看端口波形
使用配合 Keil 使用的调试助手软件 Keil Array Visualization 来查看波形 在 Keil 的 Edit->Configuration 菜单下，使能下图中的选项。

连接仿真器，烧写程序，进入调试状态。打开软件，输入端口号，点击连接。

连接成功后，输入需要查看的变量名或地址（16 进制地址）；输入需要查看的变量大小（该 大小以字节为单位）；选择数据类型；选择字节序（STM32 为小端格式）。然后点击读取即可 查看波形。也可以输入自动读取的间隔，点击读取，开始自动读取。
- 查看变量
1. 打开工程进入调试界面

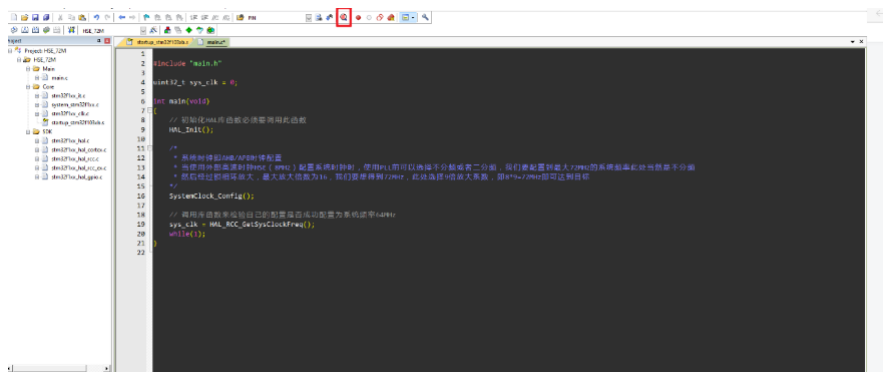
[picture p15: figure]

进入调试界面需要连接芯片
2. 选择需要查看的变量

右击选中“Add 'sys_clk' to... ”的变量,watch1，watch 都可

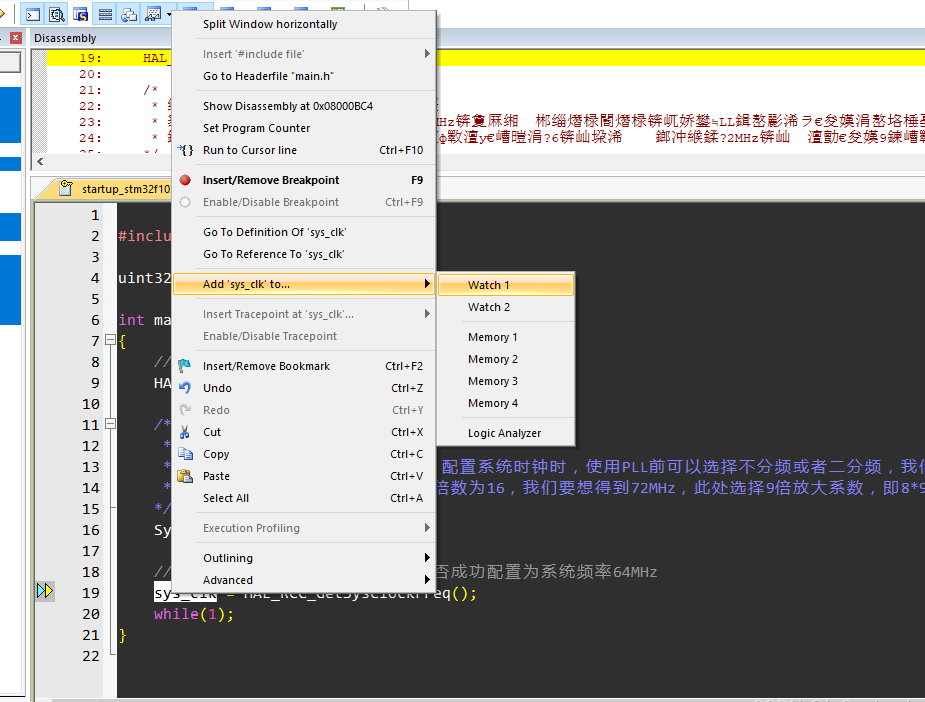
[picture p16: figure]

4、找到窗口，窗口中的值为当前变量值

5、右击 去勾√Hex 显示（16 禁止） 以十进制显示

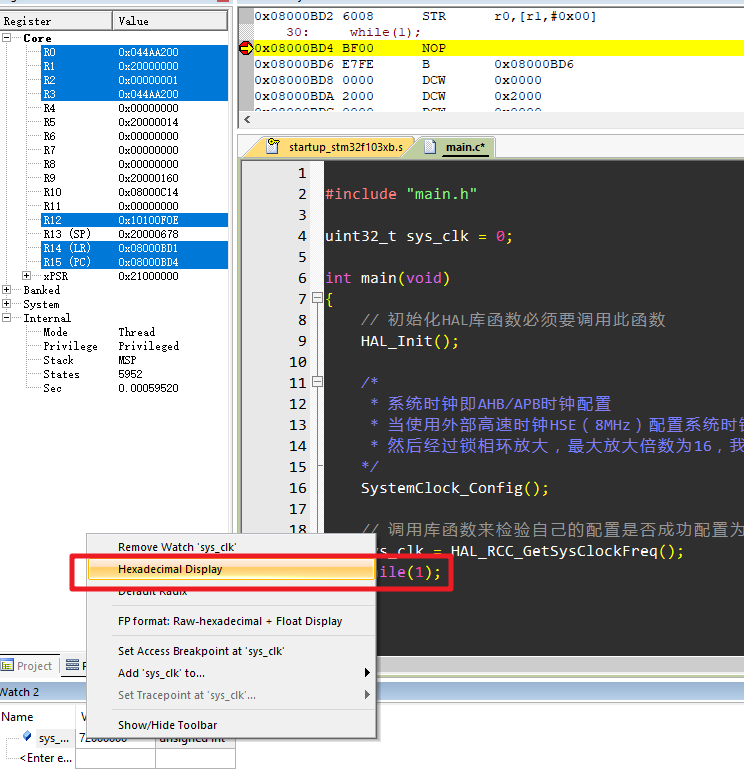
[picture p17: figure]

- 查看 IO 口状态
实现在单步执行代码时，查看硬件 IO 口电平变化和变量值的变化。先将硬件 IO 口模 拟器打开。

显示的是软件模拟出的单片机 P1 口 8 位口线的状态，单片机上电后 I / O 口全为 1,即 十六进制的 0xFF。
4.sec 查看单句运行时间！

左侧的寄存器窗口中可以到一些寄存器名称及它们的值，本小节的核心部分" sec ”，它 后面显示的数据就是程序代码执行所用的时间，单位是秒。通过添加断点，单步执行就可以 得到我们想要的时间数据。
5.添加断点

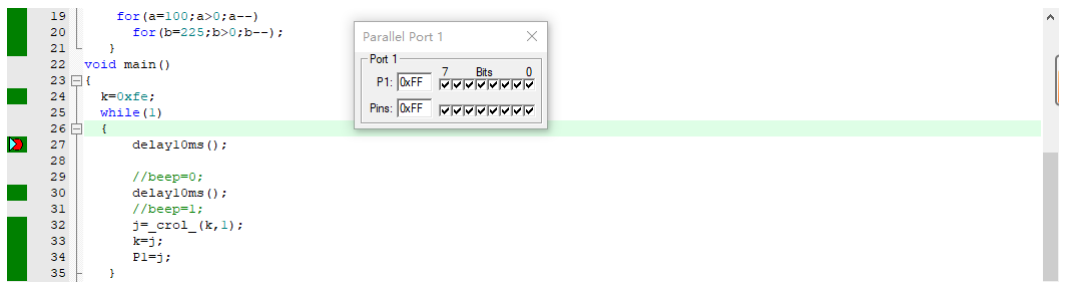
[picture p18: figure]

我们在延时函数处，添加断点，然后运行，会看到延时时间。

我们选择跳过函数，会看到时间。

# 程序实现结果

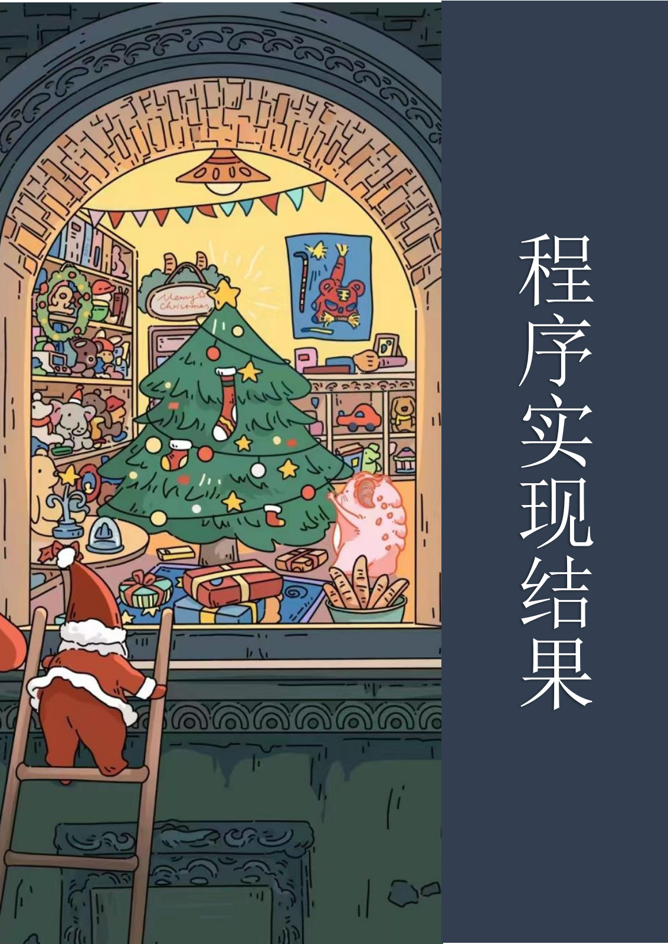
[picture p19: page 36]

## 九、程序实现结果

1、中控屏显示效果

本项目在中控板的 TFTLCD 屏幕上共进行了三个界面的绘制，分别是封面、模式一界面、

模式二界面，同时使用按键输入功能，从而在三个界面之间实现来回切换，按下一次 WK_UP

按键，即可实现一次切换，切换顺序为封面—模式一—封面—模式二—封面。

封面展示 | 模式一界面 | 模式二界面
2、列车运行效果

通过程序进行 PWM 波输出控制电机转动从而控制小车的运行状态，可通过调整其占空

比从而改变列车的运行速度，实现模拟真实的列车运行状态。

地面运行 | 轨道运行（无橡胶条） | 轨道运行（有橡胶条）

3、组合联调效果

当中控屏部分和列车轨道部分各自能够正常运行后，我们搭建整体模型联调，由于列车

具有一定长度，轨道弧度不能过大否则极易发生脱轨现象，调整合适的轨道弧度，设置合适

的信号灯与红外传感模块的位置和间距，根据项目主题搭配相宜的景观装饰后整个列车运行

模型的效果如下所示（更完整的运行效果已在视频中呈现）。

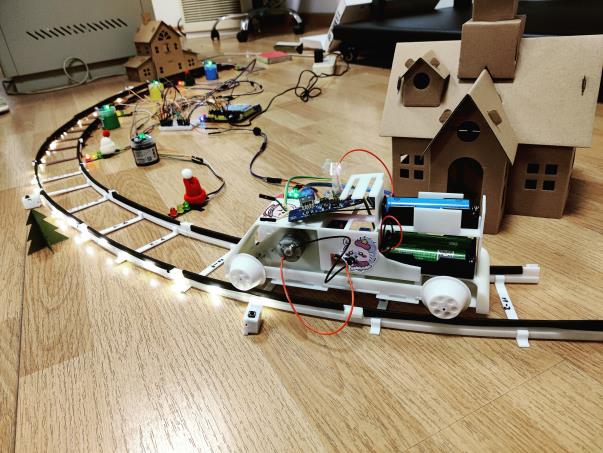
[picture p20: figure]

初次搭建效果（此时轨道尚未成环）

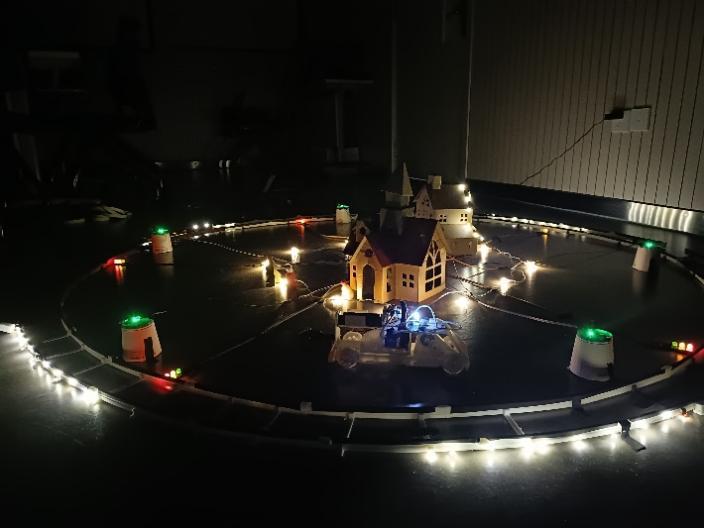
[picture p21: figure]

二次搭建效果（此时轨道已成环）

# 程序性能

## 十、程序性能

1. 代码覆盖率：

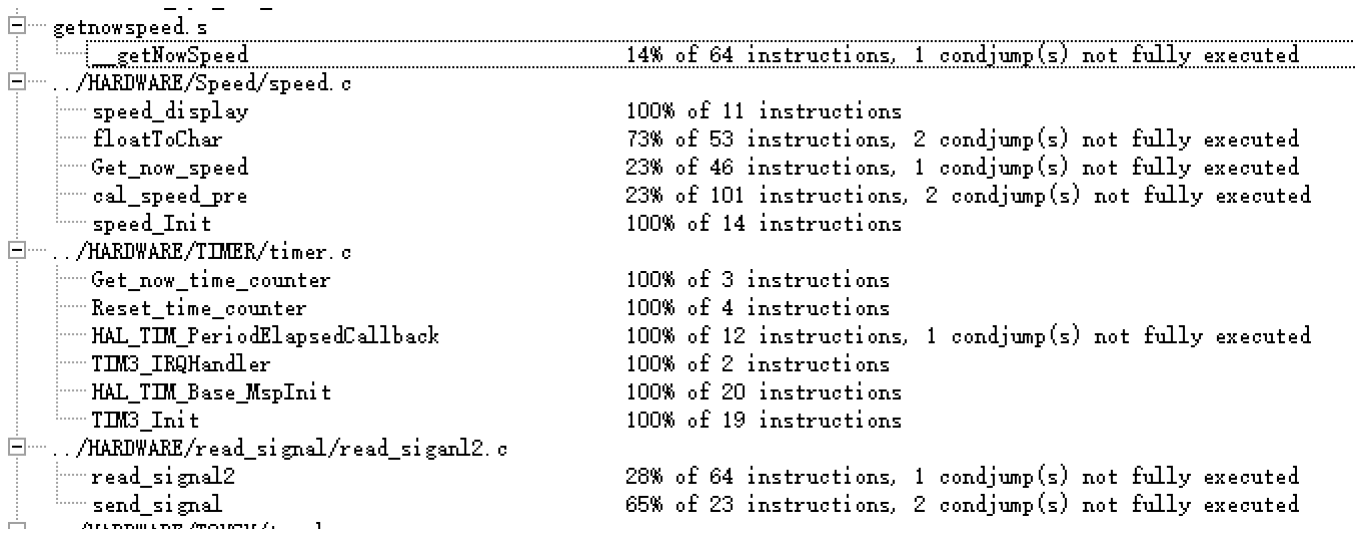
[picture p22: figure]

由于 STlink 是一款比较基础的调试器，不支持 ARM 的 ETM，因此不能一边运行程序，

一边得到真实的代码覆盖率。ETM(Embedded Trace Macrocell)，是一种硬件调试工具，是

ARM 核心中的一个重要部分。它主要被用来非入侵地跟踪 ARM 核心的执行。通过 ETM，可以

得到详细的程序执行路径，包括分支、程序计数器的值、指令的执行状态等信息。

在这种情况下，我们只能通过攥写另外的测试程序来得到一些粗略的代码覆盖率。但是

这样的话会带来两个比较严重的问题，一是由于 LCD 屏幕用到了外部内存，simulator 是不

能访问这些内存地址的，因此需要在测试代码覆盖率时将所有和 LCD 屏幕有关的所有调用

函数全部注释掉；而这也将影响得到的代码覆盖率（所有与 LCD 有关的函数都无法执行）。

二是在很多情况下，代码内部是存在各种条件分支的，由于测试例不全等情况，总会有一些

条件分支无法被遍历到，因此导致了测得的代码覆盖率远远小于真实的代码覆盖率。例如汇

编代码 getnowspeed.s 就是这样的情况。在图中的*** not fully executed***都是类似的

情况。

因此，我认为最好的解决方案是更换更好的连接器，例如 J-Link 等能够支持 ETM 的连

接器。虽然 STlink 在很多情况下能满足我们的需求了，但既然课程要求了我们测试代码覆

盖率，我认为课程老师也应该提供这样的硬件设备。

2. 时间和空间分析

本项目没有在时间和空间上较复杂的算法，因此时间复杂度、空间复杂度都可以忽略不

计。

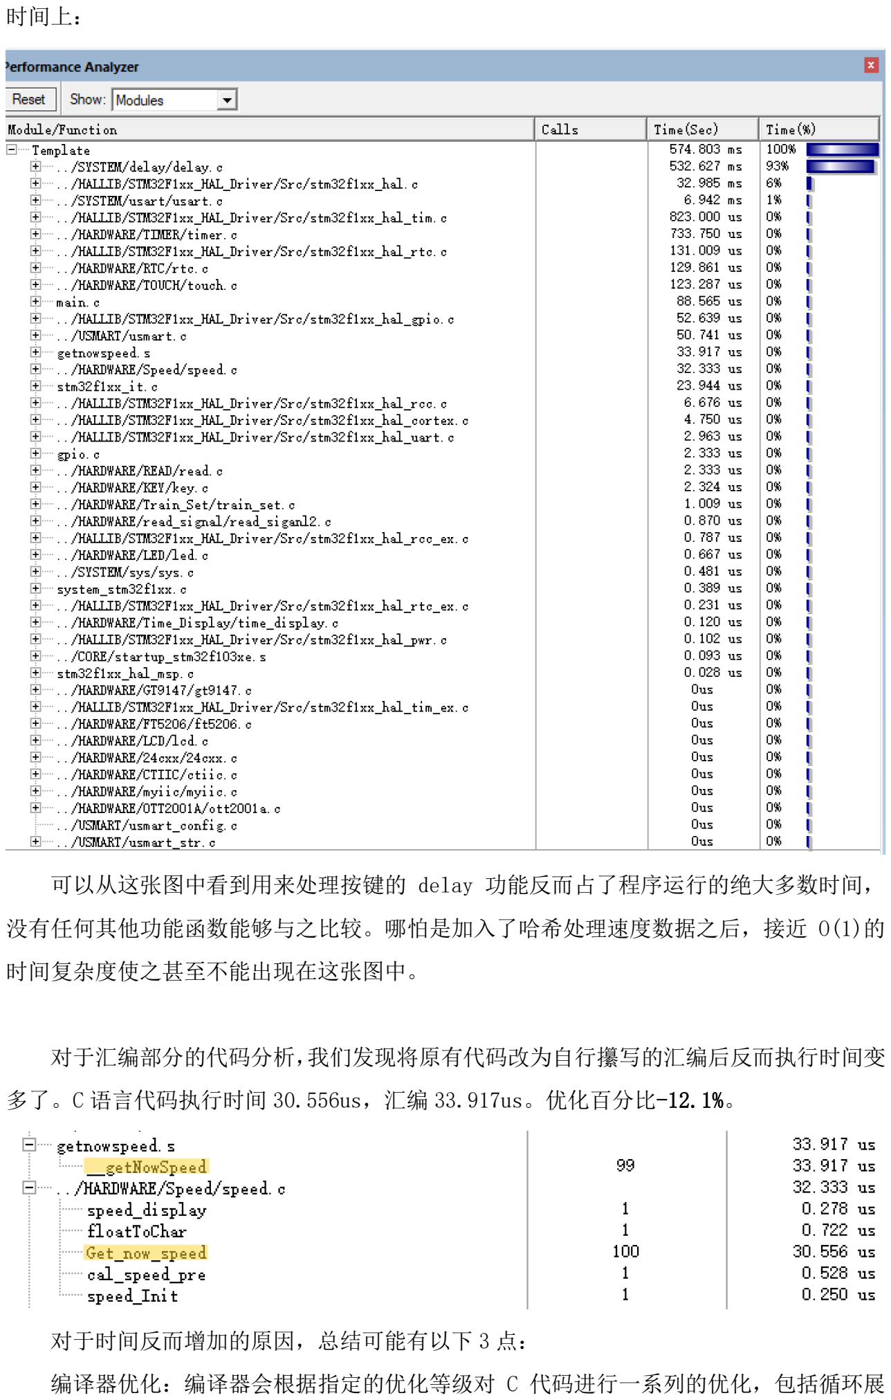
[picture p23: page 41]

时间上：

可以从这张图中看到用来处理按键的 delay 功能反而占了程序运行的绝大多数时间，

没有任何其他功能函数能够与之比较。哪怕是加入了哈希处理速度数据之后，接近 O(1)的

时间复杂度使之甚至不能出现在这张图中。

对于汇编部分的代码分析，我们发现将原有代码改为自行攥写的汇编后反而执行时间变

多了。C 语言代码执行时间 30.556us，汇编 33.917us。优化百分比-12.1%。

对于时间反而增加的原因，总结可能有以下 3 点：

编译器优化：编译器会根据指定的优化等级对 C 代码进行一系列的优化，包括循环展

开，常量折叠，消除无效计算等。这可能会使 C 代码的执行效率超过手工优化的汇编代码。

指令调度：现代 CPU 包含流水线和并行执行技术，根据代码的依赖关系，不同的指令可能会

并行执行，或者在等待数据时执行其他的指令。编译器通常会进行指令调度优化，改变指令

的顺序以提高 CPU 的利用率。如果汇编代码没有考虑这些因素，可能就会出现执行效率低的

情况。

指令选择：现代 CPU 通常包含多种实现相同功能的指令，这些指令可能在执行时间和功耗等

方面有差异。编译器会根据目标平台的特性选择最优的指令。如果手写的汇编代码没有使用

最优的指令，可能会导致执行时间增加。

空间上：

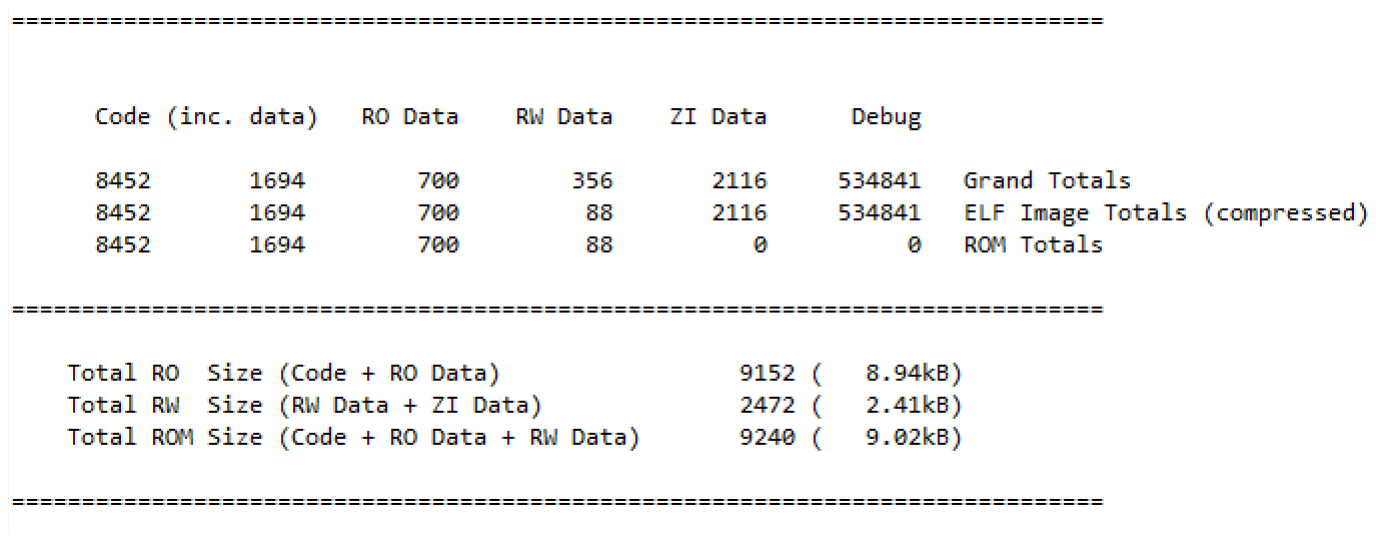
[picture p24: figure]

两张图中的第一张图是 get_now_speed()用 C 语言实现的情况下的总空间消耗，而第二

张图则是用汇编代替后的总空间消耗。可以看到二者 SRAM 的大小相同，都是 2472B，但 RO

size(Read-Only Size)不同，这代表存储在程序内存中的常量数据和代码段的大小不同。

因此可以看出 ARMCC 编译器对这部分 C 代码进行了一些优化，通过增加命令数量来得

到了更好的时间性能表现。结合之前所学的知识，极有可能的一种情况是 ARMCC 将这一部分

的计算拆解成了流水线架构，从而可以并行执行多项计算任务，从而减少了运行时间，但也

同时增加了一些用于存储命令的空间。

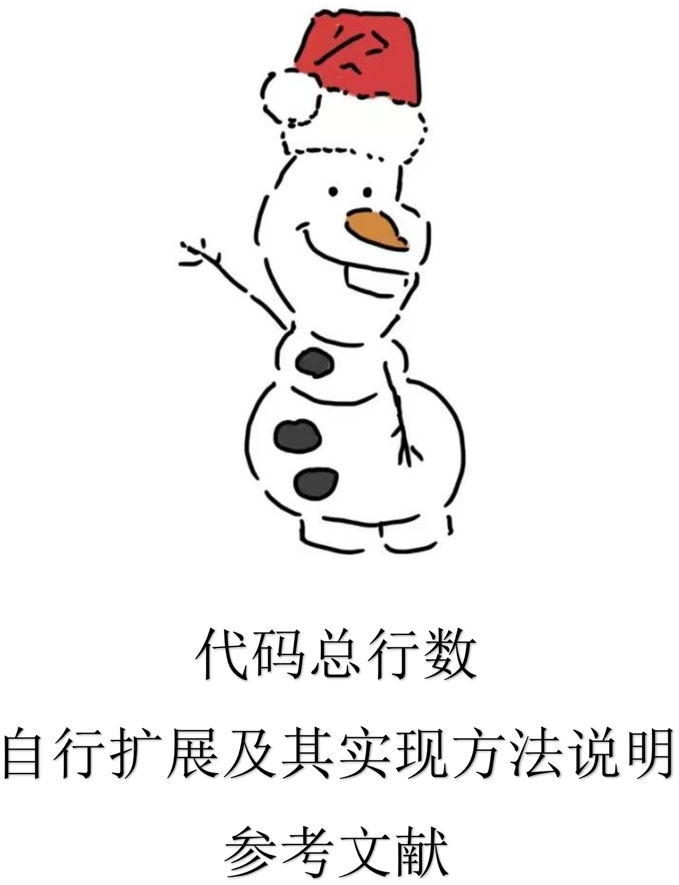
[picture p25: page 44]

# 代码总行数

# 自行扩展及其实现方法说明

# 参考文献

## 十一、代码总行数

主控板：

小车板：

（由于小车板使用的是标准库，不是 HAL 库，因此代码量计算方式有所区别）

文件名/函数名 | 行数 | 文件名/函数名 | 行数
PWM.c/.h | 60 | Serial.c/.h | 50/170
Main.c | 60 | 总代码量 | 170

## 十二、自行扩展及其实现方法说明

1. 机械部分：

1.1 减速器与电机直接融合。

1.2 两级齿轮或其他方式直接驱动。

1.3 取消轴承，直接采用松配合方式。

1.4 选用更粗的轴和杆。

1.5 小火车的长宽比减少。

2. 电路部分：

2.1 供电板。

2.2 车站部分电路（传感器、控制等）。

2.3 小火车蜂鸣器。

2.4 信号灯译码器。

3． 软件部分

3.1 实时速度哈希演算。

3.2 到站时间实时计算。

## 十三、参考文献

C++编码规范，陈世忠，人民邮电出版社，2002

文件名/函数名 | 行数 | 文件名/函数名 | 行数
Read.c/.h | 260 | Train_set.c/.h | 260
Read_signal2.c/.h | 70 | Show_picture() | 10
Speed.c/.h | 120 | Main.c/.h | 100
Time_display.c/.h | 50 | __getnowspeed() | 120(汇编)
Timer.c/.h | 10
Train_display.c/.h | 80 | 总代码量 | 1070

高质量程序设计指南：C++/C 语言，林锐等，电子工业出版社，2003

STM32F1 开发指南(精英版)-库函数版本_V1.3

陈启军，嵌入式开发及其应用

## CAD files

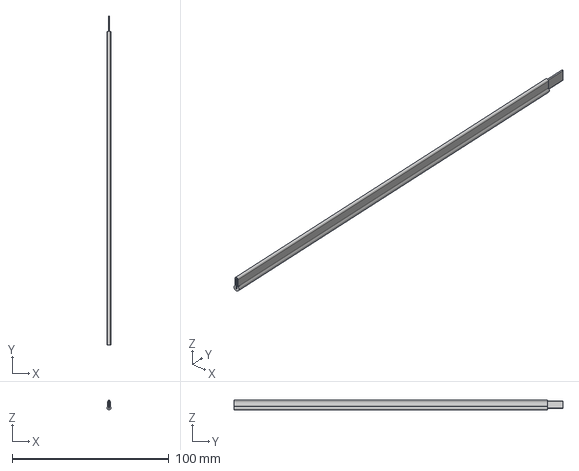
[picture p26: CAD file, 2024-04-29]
3D_design/星穷列车_轨道 v1.step
2.50 x 210.0 x 6.25 mm

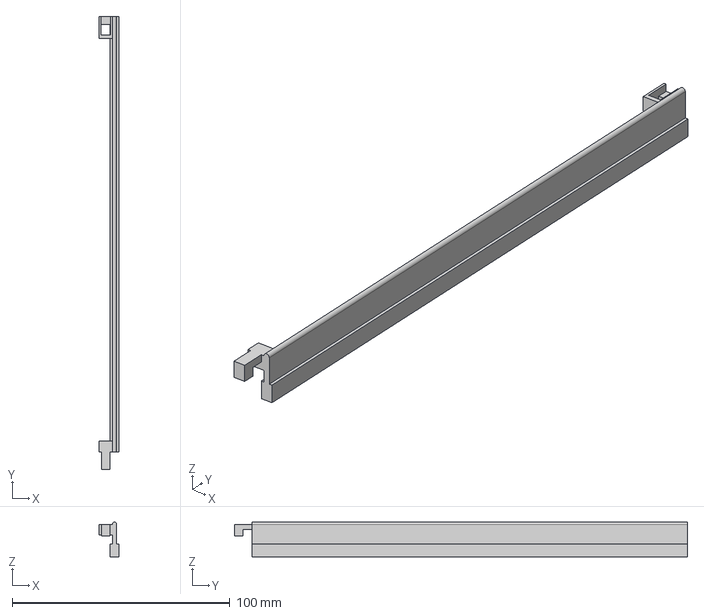
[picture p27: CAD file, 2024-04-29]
3D_design/轨道3.0 v5.step
9.00 x 208.0 x 16.0 mm

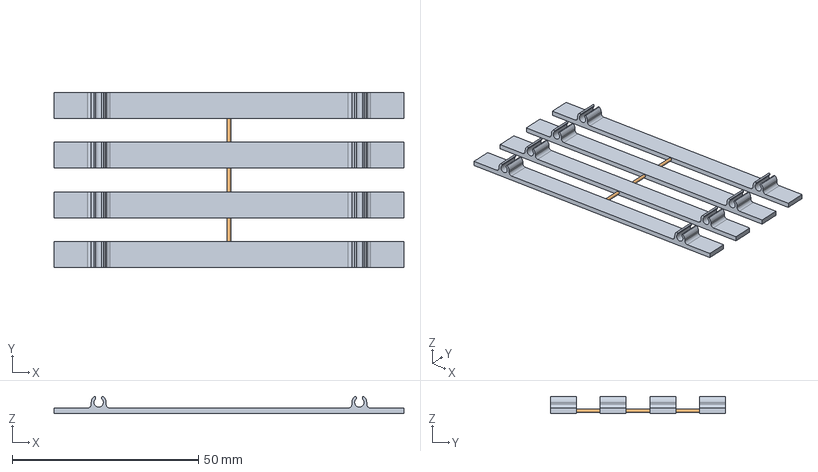
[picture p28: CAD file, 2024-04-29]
3D_design/星穷列车_铁轨木枕_加工 v3.step
94.0 x 47.0 x 4.60 mm

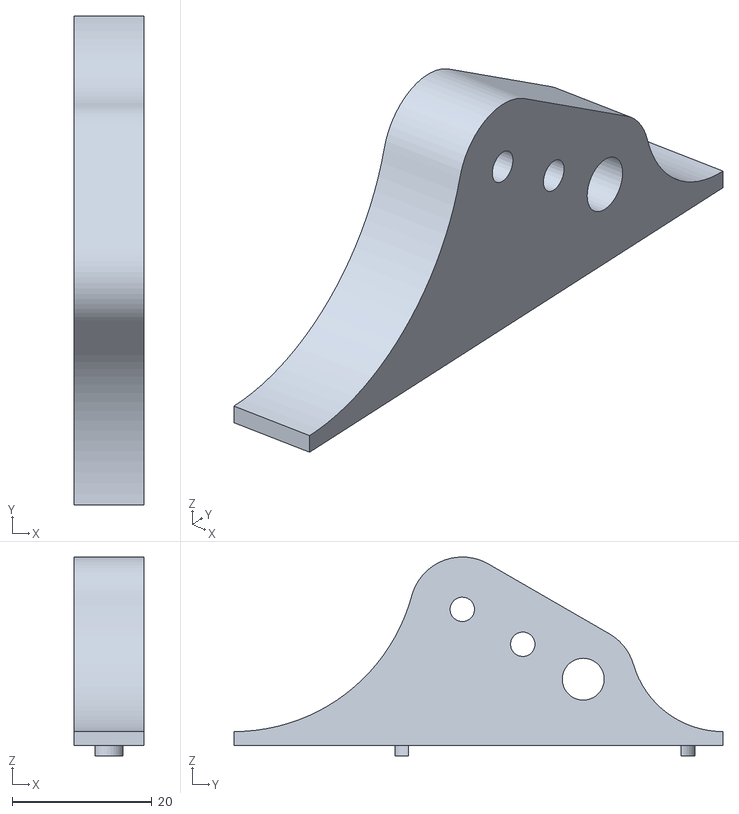
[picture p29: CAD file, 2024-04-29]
3D_design/星穷列车_轴承架 v1.stl
10.0 x 70.0 x 28.5

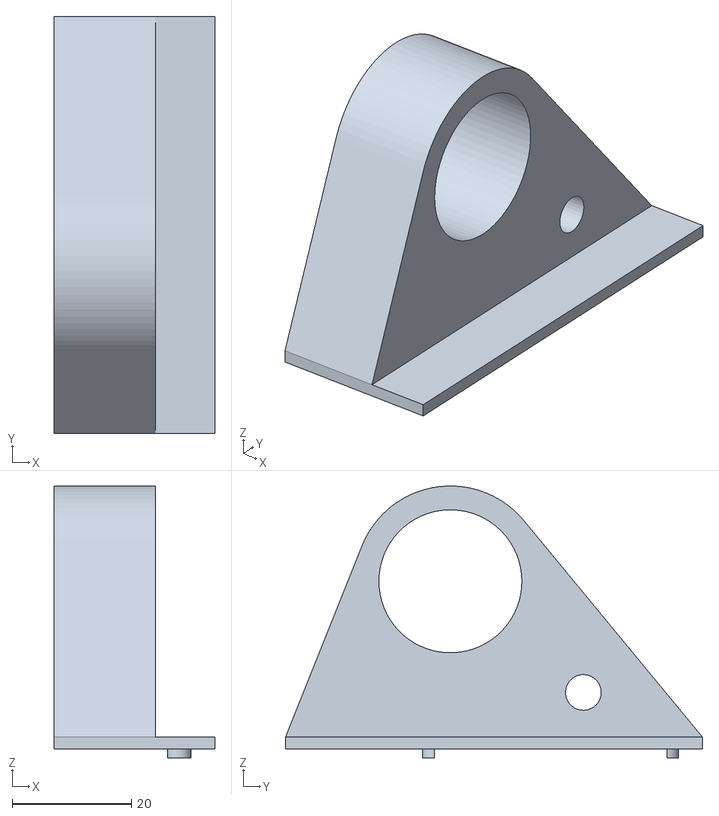
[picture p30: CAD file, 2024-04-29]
3D_design/星穷列车_电机架 v1.stl
27.0 x 70.0 x 45.7

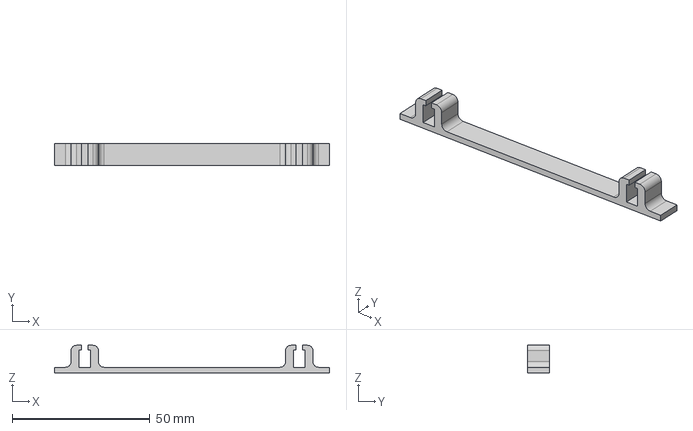
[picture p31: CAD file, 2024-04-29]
3D_design/轨道2.0_木枕 v6.step
100.0 x 8.00 x 10.0 mm

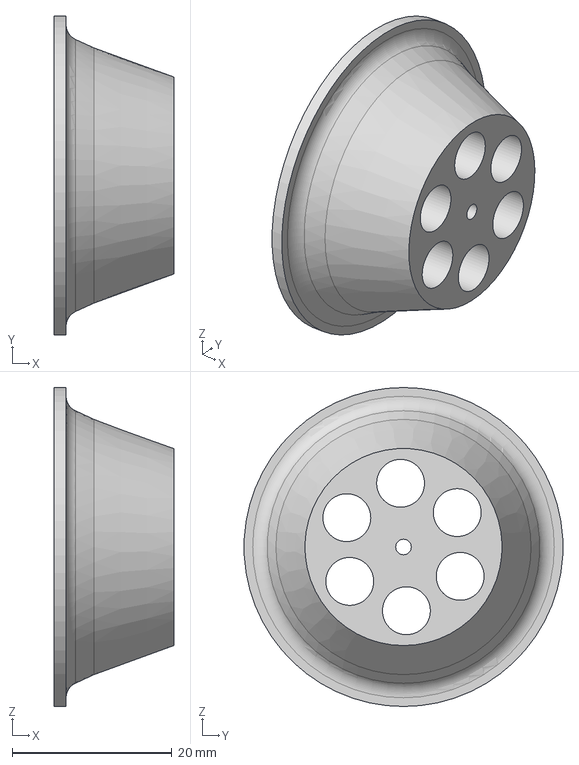
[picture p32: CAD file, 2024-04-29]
3D_design/星穷列车_右前轮 v3.step
15.0 x 39.9 x 40.0 mm

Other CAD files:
3D_design/轨道2.0_木枕 v4.step
3D_design/轨道3.0 v4.step

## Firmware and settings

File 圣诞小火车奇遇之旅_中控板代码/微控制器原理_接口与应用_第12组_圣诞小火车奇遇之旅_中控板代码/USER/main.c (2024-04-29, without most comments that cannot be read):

#include "sys.h"
#include "delay.h"
#include "usart.h"
#include "led.h"
#include "lcd.h"
#include "usmart.h"
#include "rtc.h"
#include "gpio.h"
#include "read.h"
#include "speed.h"
#include "train_display.h"
#include "time_display.h"
#include "timer.h"
#include "train_set.h"
#include "key.h"
#include "touch.h"
#include "24cxx.h"
#include "cover.h"
/************************************************
 ALIENTEK ս��STM32F103������ ʵ��15
 RTCʵ��-HAL�⺯����
 ����֧�֣�www.openedv.com
 �Ա����̣� http://eboard.taobao.com
 ��ע΢�Ź���ƽ̨΢�źţ�"����ԭ��"����ѻ�ȡSTM32���ϡ�
 �������������ӿƼ����޹�˾
 ���ߣ�����ԭ�� @ALIENTEK
************************************************/

int main(void)
{
	u8 key;
	int flag = 0;
	HAL_Init();
	Stm32_Clock_Init(RCC_PLL_MUL9);
	delay_init(72);
	uart_init(9600);
	LED_Init();
	LCD_Init();
	usmart_dev.init(84);
	RTC_Init();
	GPIO_Init();
	KEY_Init();

	TIM3_Init(1000 - 1, 72 - 1); // 1ms clock

	while (RTC_Init())
	{
		LCD_ShowString(30, 266, 200, 16, 16, "RTC ERROR!   ");
		delay_ms(800);
		LCD_ShowString(30, 266, 200, 16, 16, "RTC Trying...");
	}

	//	LCD_ShowString(40,302,200,16,16,"    -  -     ");
	//	LCD_ShowString(60,284,200,16,16,"  :  :  ");

	while (1)
	{
		//		printf("1");
		show_picture(0, 0, 240, 320, (u16 *)gImage_cover);
		key = KEY_Scan(0);
		if (key == WKUP_PRES && flag == 0)
		{
			LCD_Clear(WHITE);
			speed_Init();
			while (flag == 0)
			{
				time_display();
				cal_speed_pre();
				speed_display();
				read_signal();//Arriving time display is here
				key = KEY_Scan(0);
				if (key == WKUP_PRES)
					break;
			}
			flag = 1;
		}
		else if (key == WKUP_PRES && flag == 1)
		{
			LCD_Clear(WHITE);
			LCD_DrawRectangle(2, 34, 238, 252);
			LCD_DrawRectangle(2, 252, 238, 280);
			tp_dev.init();
			while (flag == 1)
			{
				read_signal2();
				time_display();
				train_set();
				light_set();
				speed_set();
				key = KEY_Scan(0);
				if (key == WKUP_PRES)
					break;
			};
			flag = 0;
		}

		//		if(t!=calendar.sec)
		//		{
		//			t=calendar.sec;
		//			LCD_ShowNum(40,302,calendar.w_year,4,16);
		//			LCD_ShowNum(80,302,calendar.w_month,2,16);
		//			LCD_ShowNum(104,302,calendar.w_date,2,16);
		//			switch(calendar.week)
		//			{
		//				case 0:
		//					LCD_ShowString(136,302,200,16,16,"Sunday   ");
		//					break;
		//				case 1:
		//					LCD_ShowString(136,302,200,16,16,"Monday   ");
		//					break;
		//				case 2:
		//					LCD_ShowString(136,302,200,16,16,"Tuesday  ");
		//					break;
		//				case 3:
		//					LCD_ShowString(136,302,200,16,16,"Wednesday");
		//					break;
		//				case 4:
		//					LCD_ShowString(136,302,200,16,16,"Thursday ");
		//					break;
		//				case 5:
		//					LCD_ShowString(136,302,200,16,16,"Friday   ");
		//					break;
		//				case 6:
		//					LCD_ShowString(136,302,200,16,16,"Saturday ");
		//					break;
		//			}
		//			LCD_ShowNum(60,284,calendar.hour,2,16);
		//			LCD_ShowNum(84,284,calendar.min,2,16);
		//			LCD_ShowNum(108,284,calendar.sec,2,16);
		//			LED0=!LED0;
		//		}
		//		delay_ms(10);
	};
}

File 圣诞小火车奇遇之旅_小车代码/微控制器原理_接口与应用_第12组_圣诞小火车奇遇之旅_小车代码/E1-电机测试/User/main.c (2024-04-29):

#include "stm32f10x.h" // Device header
#include "Delay.h"
#include "OLED.h"
#include "PWM.h"
#include "Serial.h"
#include "stm32f10x_gpio.h"
uint8_t i;
uint32_t dutycycle = 0;
uint8_t RxData;
#define MaxdutyCycle 950
#define MindutyCycle 250
int main(void)
{
	// Initialize PWM channels with a period of 1000 and a prescaler of 72
	TIM3_PWM_Init(1000, 72);		   // PA6,PA7
	PWM_SetCompare1(1000 - dutycycle); // PA6
	Serial_Init();
	GPIOs_Init();
	while (1)
	{
		if (Serial_GetRxFlag() == 1)
		{
			RxData = Serial_GetRxData();
			switch (RxData)
			{
			case '+':
				dutycycle += 50;
				if (dutycycle > MaxdutyCycle)
					dutycycle = MaxdutyCycle;
				PWM_SetCompare1(1000 - dutycycle);
				// LED1_Turn();
				break;
			case '-':
				dutycycle -= 50;
				if (dutycycle < MindutyCycle)
					dutycycle = MindutyCycle;
				PWM_SetCompare1(1000 - dutycycle);
				// LED1_Turn();
				break;
			case 'S':
				dutycycle = 0;
				PWM_SetCompare1(1000 - dutycycle);
				// LED1_Turn();
				break;
			case 'P':
				dutycycle = 400;
				PWM_SetCompare1(1000 - dutycycle);
				// LED1_Turn();
				break;
			case '2':
				GPIO_SetBits(GPIOC, GPIO_Pin_13);
				break;
			case '3':
				GPIO_ResetBits(GPIOC, GPIO_Pin_13);
				break;
			default:
				break;
			}
		}
	}
}
